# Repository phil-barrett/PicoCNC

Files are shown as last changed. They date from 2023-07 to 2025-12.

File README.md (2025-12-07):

# PicoCNC

## Now fully open source
I have released the full V1.55eth design files under the MIT open source license. Please post your usage and derivations in the [Discussions Section](https://github.com/phil-barrett/PicoCNC/discussions).

## older readme.
No longer available for purchase.

A breakout board that, along with grblHAL and a Rapsberry Pi Pico microcontroller, creates a powerful CNC motion controller for devices like routers, mills, lasers and lathes.  Using grblHAL, it forms the basis of a motion control system with advanced features.

[System builder's Resources](https://www.grbl.org/resources)

[User Manual](https://github.com/phil-barrett/PicoCNC/blob/main/PicoCNC%20User%20Manual.pdf)

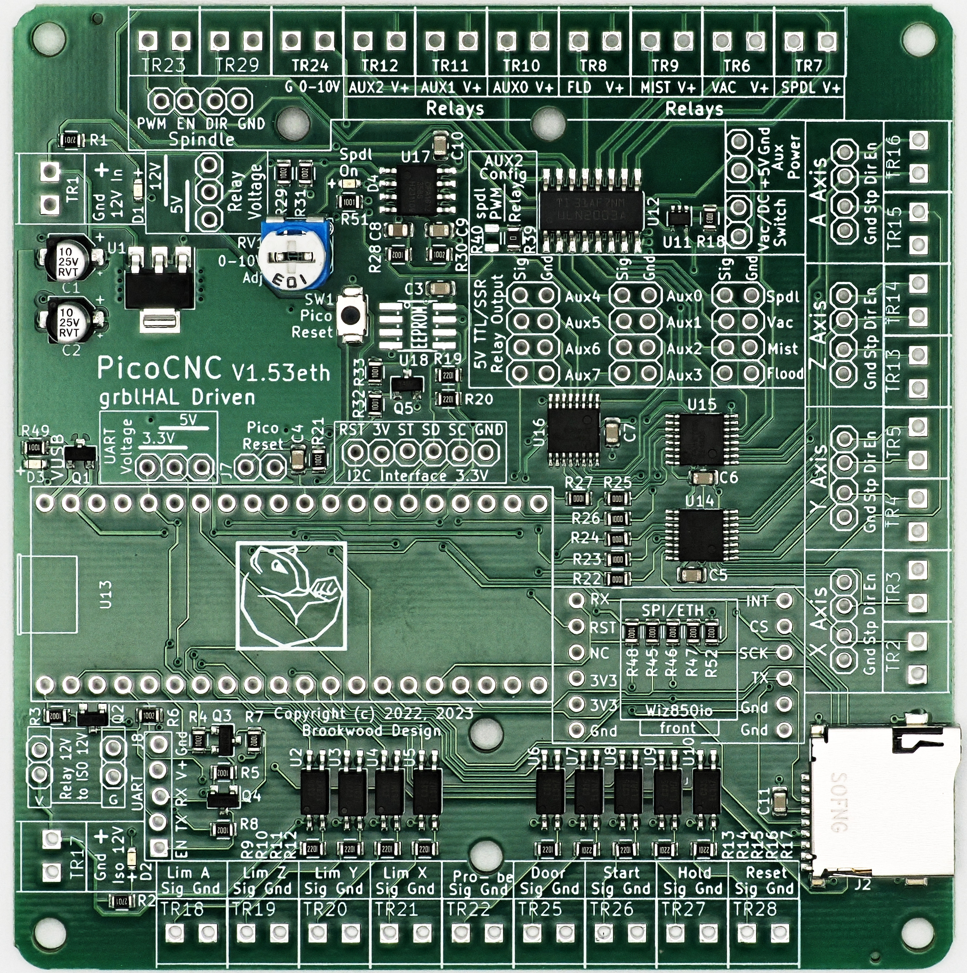
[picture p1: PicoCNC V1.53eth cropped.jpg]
PicoCNC


Key features of the PicoCNC board.
* Supports up to 4 Axes via Screw Terminal and Pin Header.
* Spindle control.
  - PWM (5V).
  - Direction (5V).
  - 0-10V.
  - 12V PWM supported (via open collector output).
* Limit Switches for each axis.
  - Supports switches or powered proximity sensors.
  - 12V for better EMI immunity.
  - Separate power input for full isolation
  - Opto-isolated
* Relay support
  - Directly drive up to 7 relay coils via open collector outputs.
  - Relay Coil voltage selectable between +5V or +12V.
  - Drive up to 11 SSR or Logic Level relays.
* Isolated standard Grbl input controls: Cycle Start, Feed Hold, EStop and Safety Door. Opto-Isolated.
* Opto-Isolated Probe input.
* Supports both Pico and Pico W.
* Comunications.
  - USB (via Pico and Pico W)
  - WiFi (via Pico W)
  - Ethernet (via Wiz850io Ethernet Module)
* Micro SD Card socket.  Allows storage of GCode programs.  GCode programs may be run from the SD Card.
* Dust Collection support.
  - Dust Collection relay and TTL output ganged to Spindle. 
  - Header for a switch to manually run Dust Collector.
* Flexible power input.  Two 12V sections, one for Stepper/Servo output, relays and spindle control, one for isolated limit, probe and control inputs. The two sections may be joined for the budget conscious builder. On board 5V generation.
* LED indicators for 12V inputs, +5V and spindle active.
* Open collector outputs allow adding pull-up resistors on the board.
* Expansion headers for I2C, SPI and UART.  UART 3.3V/5V translation supported.
* Powered by open source software - grblHAL.

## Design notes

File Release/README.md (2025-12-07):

## MIT License release of PicoCNC design files.

Copyright (c) 2023, 2025 Phillip L. Barrett

Permission is hereby granted, free of charge, to any person obtaining a copy
of this software and associated documentation files (the "Software"), to deal
in the Software without restriction, including without limitation the rights
to use, copy, modify, merge, publish, distribute, sublicense, and/or sell
copies of the Software, and to permit persons to whom the Software is
furnished to do so, subject to the following conditions:

The above copyright notice and this permission notice shall be included in all
copies or substantial portions of the Software.

THE SOFTWARE IS PROVIDED "AS IS", WITHOUT WARRANTY OF ANY KIND, EXPRESS OR
IMPLIED, INCLUDING BUT NOT LIMITED TO THE WARRANTIES OF MERCHANTABILITY,
FITNESS FOR A PARTICULAR PURPOSE AND NONINFRINGEMENT. IN NO EVENT SHALL THE
AUTHORS OR COPYRIGHT HOLDERS BE LIABLE FOR ANY CLAIM, DAMAGES OR OTHER
LIABILITY, WHETHER IN AN ACTION OF CONTRACT, TORT OR OTHERWISE, ARISING FROM,
OUT OF OR IN CONNECTION WITH THE SOFTWARE OR THE USE OR OTHER DEALINGS IN THE
SOFTWARE.

## Usage Notes

### KiCAD Files
These were created with KiCAD V8.0

They are released with the intent of using JLCPCB to manufacture the PCB and 
assemble them into a working circuit board. The directory production/ includes full gerbers (PicoU4XBB.zip), 
Bill of Materials including JLCPCB library part numbers (bom,.csv) and Centroid PnP (positions.csv).

### KiCAD plugins required
To create JLCPCB files after modifying the design, you will need the Fabrication Toolkit plugin. It is 
available in the KICAD Plugin and Content Manager.

### JLCPCB Library part numbers
These were current as of June 2025.  You may need to change due to out of stock parts.

## Questions, reports, suggestions

Please use the [Discussions section](https://github.com/phil-barrett/PicoCNC/discussions/34) to ask questions, report your progress or make suggestions.

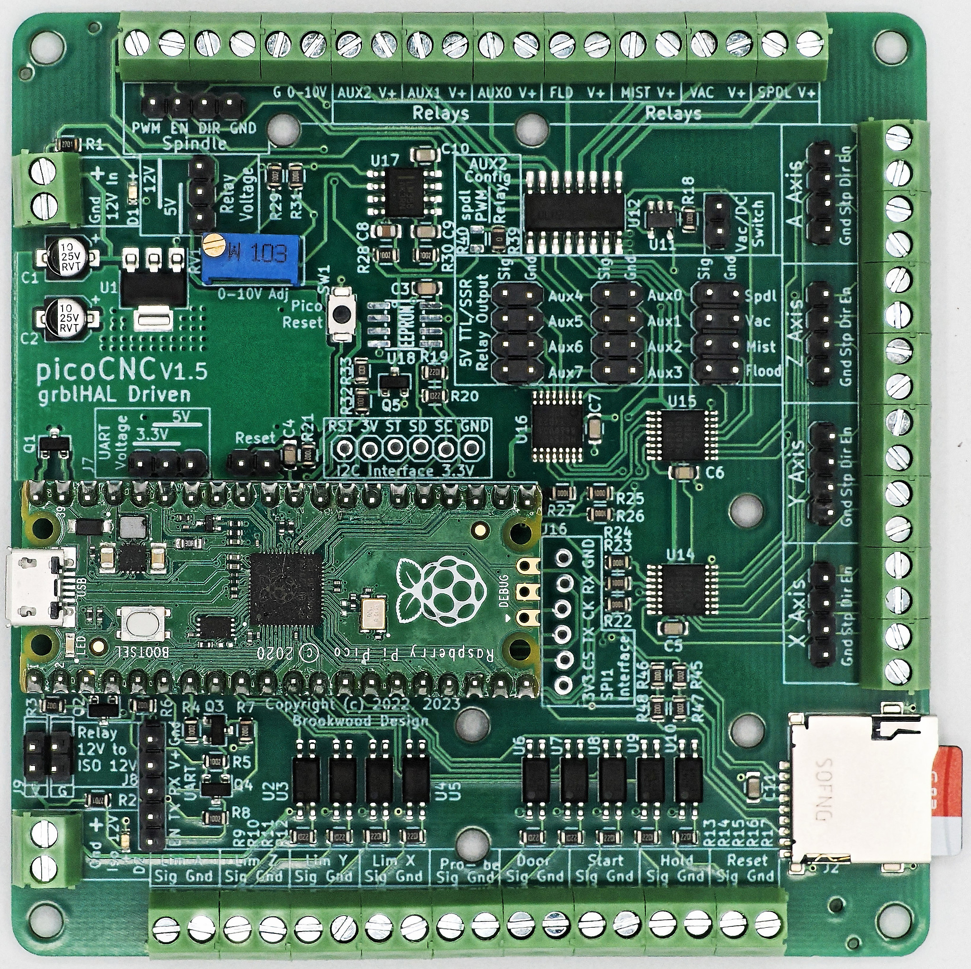
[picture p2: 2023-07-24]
PicoCNC.jpg

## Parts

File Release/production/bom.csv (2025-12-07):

Designator | Footprint | Quantity | Value | LCSC Part #
C1, C2 | 0805 | 2 | 10u | C15850
C10, C11, C3, C4, C5, C6, C7, C9 | 0805 | 8 | 100n | C49678
C8 | 0805 | 1 | 1uF | C28323
D1, D2, D3, D4 | 0805 | 4 | LED | C2297
J2 | sdcard_sofng_c111196 | 1 | MicroSD-MGnd | C111196
Q1 | SOT-23-rct | 1 | DMG2305UX-7 | C150470
Q2, Q3, Q4 | SOT-23-rct | 3 | BSS138 | C40912
Q5 | SOT-23-rct | 1 | MMBT3904 | C20526
R1, R2 | 0603 | 2 | 2K7 | C17530
R10, R11, R12, R13, R14, R15, R16, R17, R19, R20, R9 | 0603 | 11 | 2K2 | C17520
R18 | 0603 | 1 | 100K | C149504
R21, R28, R29, R3, R30, R31, R4, R45, R46, R47, R48, R5, R6, R7, R8 | 0603 | 15 | 10K | C17414
R22, R23, R24, R25, R26, R27 | 0603 | 6 | 100 | C17408
R32, R33 | 0603 | 2 | 1K | C17513
R39 | 0805 | 1 | 0 | C17477
R49, R51 | 0603 | 2 | 1K | C17530
R52 | 0603 | 1 | 4K7 | C17414
RV1 | RM065-trimmer | 1 | 10K pot | C5205021
SW1 | TA-1088R-02026 | 1 | SW_SPST | C455280
U1 | SOT-223-3_TabPin2 | 1 | AMS1117CD-5.0 | C277893
U10, U2, U3, U4, U5, U6, U7, U8, U9 | EL3H7-G | 9 | EL3H7-G | C92243
U11 | SOT-353_SC-70-5 | 1 | 74LVC1G32 | C460530
U12 | SO16 | 1 | ULN2003AD | C7512
U14, U15, U16 | HTSSOP-16_4.4x5mm_P0.65 | 3 | 74HCT595 | C460504
U17 | SO08 | 1 | LM358D | C2683482

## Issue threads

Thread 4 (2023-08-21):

D1 LED getting too much current

iLoveAndyBaker, 2023-08-21:
Minor nit-pick here, it seems like D1 and D2 are getting too much power (forward voltage is 2.71V), at least compared to the other LEDs on the board.  R1 and R2 are 2.7K, same as the resistor on all the other lines, but it's getting 12V and not 5V/3.3V etc.

D3 and R49 seem like a much happier combination at the lower voltage, the drop across it while on is 2.53V

phil-barrett, 2023-08-21:
Thanks for the note.  I believe all the LEDs are quite happy at their current levels.

While D1 and D2 do get more current than D3 and D4, (3.4 mA and 2.3 mA respectively) they are all well below the Max If of 25 mA for the 9-217/GHC-YR1S2/3T LED.  And, all 4 are well below the If they use for the specs (20 mA).  These modern LEDs are amazingly efficient. Back in the bad old days you had to pull 20 mA just to get a dim glow!
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

I had originally used 680 ohms for D3 and D4 which yields an If of 3.4 mA, I found that 1K gives about the same brightness level. This allows me to reduce the number of unique BOM items. Since I use a lot of 1K resistors, it makes the BOM cost slightly lower.

There are several other examples of BOM engineering in this board but I will leave it to others to find...

Closed 2023-08-21.

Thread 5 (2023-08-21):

U11 magic smoke and fire, Pi Pico W dead

iLoveAndyBaker, 2023-08-21:
U11 smoked, quite dramatically.  There is not and never was anything on the vac or dust collector.

Had steppers on X,Y,Z (with current limiting resistors on the step and direction pins) and only microswitches on X,Y,Z limits and a wire across reset.

Clean desk.

This is the second Pi Pico that this PicoCNC killed.

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

I suspect power issues on the board - , I haven't looked at the schematic however.  There was power cycling, I think it was probably my 12V (checked to 12.1V) supply resetting for an over-current situation until the chip got hot enough to go incandescent and stink up the whole room.  Thank god for the FR in FR4.

Things have been a little odd with powering it (can't really nail it down now that it's blowed up) but having to do weird power cycles here and there.

Please double check your power. Are we powering the Pico with the PicoCNC AND USB? Is Q1 working right? Did Tindie put the right part down?

phil-barrett, 2023-08-21:
Wow.  That's pretty dramatic.  I've been testing a number of these boards running on 12V power for a lot of hours and never had anything blow at all.  That device (74LVC1G32) runs on +5V and the pin that is burnt is the +5V pin.  Bad chip?  Maybe 12V got onto the 5V rail?  Could you show me a picture of the entire board?

Please return the board and we will refund your purchase.

iLoveAndyBaker, 2023-08-21:
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

Let me know where to mail it and I'll get it out soon.

phil-barrett, 2023-08-21:
Phil Barrett
76 Olympic Dr NW
Shoreline, WA 98177

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

phil-barrett, 2023-08-22:
I have been looking at the design for how this could happen and I really can't see anyway for that part to go short unless it was a bad part.  This circuit is in two designs with over 1100 units in the field and no reports of a problem.  I see several possibilities - 1) bad chip with an internal short (very rare), 2) shorting across the output (not obvious from the photos) or 3) chip damaged due to 12V across the 5V rail (hard to do accidentally).

iLoveAndyBaker, 2023-08-22:
Nothing, huh? Yeah I don't know either. Maybe something etched weird. Maybe a part was just bad, or wrong, or just randomly latched up. Either way, it's in the mail, I've thrown in the blown Pico as a bonus. I hope you can learn something from it, it looks like a nice little board. I would have liked to have put the FLIR camera on it, but as luck would have it, I've lent it out.

Thanks,

Andy

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

phil-barrett, 2023-08-30:
I got the board and did some poking. Powered it up with 12V.  The first thing that became clear is there was 11V on the 5V rail.  That pretty much blew all the 5V logic chips and the Pico.  I'd guess U11 being so small, it went first.  Looking at the 5V regulator U1 (AMS1117-5), I could see some damage to it. See the photo. (I made the scratch probing at it.) It failed with a direct short which is unusual - they usually die open. Maybe it took too much current and blew. Maybe too high voltage was applied - 24V would have killed it. Maybe reversed polarity? I looked at all the boards I have in stock (55) and none of them showed any damage to the regulator.  I desoldered the dead regulator and soldered a new one in place.  It happily produced 5V and did not overheat.  I did not see any evidence of over current any other place than U1 and U11.  So, it's hard to say what damaged U1.  I desoldered U11 and inspected the traces under it.  They appear to be ok so it wasn't a board short.  I also looked at the pin headers used to join the 2 12V sections to see if the shorting plugs had been installed wrong but did not see any damage.

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

So what did I learn from this?  To be honest, not a lot. A lot of this circuitry is the same as on the Teensy board. And the circuit is pretty straightforward. There is no obvious design flaw. I am thinking of adding an in line rectifier before the 12V input of the AMS1117 to at least protect it from reverse polarity though that has implications on the 0-10V circuit.  I had already separated the headers for joining the 2 12V sections to prevent accidental shorting (that's in V1.51, the currently shipping board). I am adding warnings to the User Manual about reverse polarity and power sources above 12V.

Anyway, I believe this is an isolated case.  There have been no other reports of a similar nature and in all the testing I never saw any significant overheating (I do a lot of thermal measurement on the boards during testing). In general, the worst case temperature increase is 15C over ambient, well within expectations.

Anyway, I have issued a full refund. Sorry this happened.
Phil Barrett

iLoveAndyBaker, 2023-08-30:
I'd be happy to take a new one to be honest. It makes my wiring a lot cleaner too.

The power supply was a nice switching wall wart putting out clean 12.1V.  It was running well, I connected it when I started the project and never looked back. As to why I was thinking those LEDs too bright, maybe it was that regulator after all. At any rate, I can use a different PSU.

I've seen people put big fat diodes across the input.. blows the fuse in the PSU if you go backwards, and no voltage drop that way. Provided it's got a fuse that is.

Thanks for looking into this.

Andy Baker
Red 6
________________________________
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

phil-barrett, 2023-08-30:
With the refund, you could place another order. Tindie is prompt about refunds.

phil-barrett, 2023-09-02:
I'm closing this. There have been no more reports of anything similar so I am calling a one-off problem. If anything comes up I will reopen.

Closed 2023-09-02.

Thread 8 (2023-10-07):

BOM?

pixelwaster, 2023-10-07:
The parts list on page 33 is missing. I would like to experiment with this controller.

Michael

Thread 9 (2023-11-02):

Brake Out Board for Blackpill (STM32F411CE - WeAct Studio)

wolfgangbregel, 2023-11-02:
Hello Phill,

I much appreciate your work and the well designed BOBs for Pico and Teensy.

Just a proposal: Why not consider the low cost Blackpill (STM32F411CE - WeAct Studio) as a controller base?

* Well supoported by GRBL HAL (Flawless compile with STM32Cube Ide - or GRBL Web builder)
* Just enough GPIOs (a total of 32 +2 used for SW-JTAG)  for a 4 or 5 axis CNC including per axis limit switches and inputs for Safety Door, Feed Hold, Cycle Start, Reset E-Stop and Probe
* Outputs for Spindle (Dir, Enable, PWM), Coolant Flood and Mist
* Optional inputs for Spindle Pulse / Index
* No need for external serial->parallel Expander chips at high speed clocks
* Integrated USB CDC
* Works just fine on my CNC metal milling machine (On my home brew breakout board for now)
* Plenty of headroom in Ram amd Flash for extensions and future development

Many thanks for considering,

Wolf

phil-barrett, 2023-11-02:
Thanks for the input.  As usual, there are always trade-offs to be taken into account. Such is engineering...

I've considered the Black Pill before and it would be a very reasonable choice on many fronts.  One problem is that Chinese suppliers often change components without any notice.  This includes the actual processor (there are a number of F411 clones out there that MOSTLY work the same as the STM part).  Also, the availability of the Black Pill is highly variable. I have looked at using the F411 directly on a base board but the chip shortage hit the STM32 line very hard. The RP2040 never had that problem and it is a consistent product, never any silent changes. As we emerge from the still lingering effects of the shortage, I will continue to re-evaluate things.

The main difference is that the PicoCNC board only supports 4 Axes. The PicoCNC step output rate is well above 200 KHz, supports WiFi, doesn't need a programmer and is super inexpensive.  Not suitable for lathes, though. And, soon I will release a PicoCNC that will support Ethernet.  A Blackpill based board with Ethernet would probably not be able to support 5 Axes in that case.

wolfgangbregel, 2023-11-02:
Hello Phil,

Yes, I fully understand your concerns as to chinese suppliers and their
liberty in changing specs and/or chips.
And yes the Pico is well documented and more consistent over time since its
appearance.
I want to replace an Arduino based control board (i.e. no interference
protection - but no EMC problems either) in order to have a 4th axis and
backlash compensation.
So - I'll order one of your PicoCNC boars shortly. I just had a few really
annoying surprices from the German customs dept. I.e. calling for next to
half of the invoice as import tax for electronics received from the US.

Greatings and thumbs up from Germany

Wolfgang

On Thu, Nov 2, 2023 at 4:44 PM phil-barrett ***@***.***>
wrote:

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

phil-barrett, 2023-11-02:
Thanks!  I have a lot of German customers, it is my second biggest market (after USA), and have not heard them complain about getting nicked for customs/duty/VAT. I do supply correct documentation including price so the max should be a 20% charge, I think. (I will admit, it's hard to keep track of it.) Maybe they just don't tell me. Note, I use the US postal system which hands off to Deutsche Post and not carriers like FedEx or UPS. The few times I have used UPS internationally they not only hit the customer for Duty/VAT and ignored the listed price but also added a $30 or so brokerage fee. One Irish customer was charged $70 on a $70 order. Thieves.

wolfgangbregel, 2023-11-03:
Hello Phil,

many thanks for your info. Indeed, Deutsche Post/DHL is the most reliable,
honest and mostly cheapest service here in Germany.
Good to hear that US postals works with DHL only.
I once had an experience with UPS for an order I accidently placed with
DigiKey US. I had to pay about $20 service fee on the $50 order - heavy
(plus VAT of course).

So i checked for orders from the US to Germany *below *€150 (*above *is
different):

Duty: None
Import VAT: 19% (on the invoice total, incl. transport!)
DHL service fee: €6

Just for info, in case someone asks.

I'll order a PicoCNC via Tindie shortly.

Many thanks for the great job!

Best regrards, Wolfgang

On Thu, Nov 2, 2023 at 8:35 PM phil-barrett ***@***.***>
wrote:

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

wolfgangbregel, 2023-11-03:
Hello Phil,

just to let you know: I just ordered a PicoCNC assy kit via Tinide.

Best regards, Wolfgang

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

phil-barrett, 2023-11-03:
Thank You.

You should have email confirmation and the package will ship in about 1 hour.

Phil

wolfgangbregel, 2023-11-03:
Hello Phil,

yes, just received a confirmation from US postal.

Many thanks, Wolfgang

On Fri, Nov 3, 2023 at 5:47 PM phil-barrett ***@***.***>
wrote:

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

Closed 2024-02-16.

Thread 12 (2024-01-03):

Best way to buy from Europe (Italy)

yaapu, 2024-01-03:
Hi Phil,
I'd like to get one of your PicoCNC boards, I tried tindie but the only shipping option is "United States Postal Service Standard Ground Rate (No Tracking)", I'd rather use a tracked service since custom duties are involved, do you have any hints/ideas?

phil-barrett, 2024-01-03:
Actually, you will get tracking with that service.  I should revisit the tindie shipping setup.

phil-barrett, 2024-01-03:
Fixed it.  Now it says tracking.

Note that this is a US Postal Service tracking number and may not give you tacking within Italy.  I have seen cases in a number of countries where tracking is not updated after the hand over to the local postal service.  And, I have seen cases where a given country's tracking is inconsistent - sometimes they do it but other times they don't.  Very annoying and there is no recourse.  Sorry, I wish it was better.

Phil

yaapu, 2024-01-03:
Thanks for your super quick reply, I suspect that international orders will not use Ground Service, do you have an idea of which tracked service will be used?
Any track record of how long it would take to get it to italy or europe?

phil-barrett, 2024-01-03:
USPS hands the package off to whatever the designated carrier is for the end country.  Usually it is the national mail carrier but I don't have any visibility into that.

Ship time to EU countries can vary a lot.  1 week to 4 weeks. The last several I shipped to Italy ranged between 13 and 17 days. Once the package gets to Italy, it appears to take just a few days.  The biggest delay for international shipping is the gap between the last US reported location and the first end country location.  That is between 3 and 10 days, typically.

yaapu, 2024-01-03:
Thanks Phil

Closed 2024-01-03.

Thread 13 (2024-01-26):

When will you get the assembly kit back in stock?

rgfx, 2024-01-26:
Sorry for posting here. I want to order one of these but have the kit would be nice. I can wait.

phil-barrett, 2024-01-26:
Oops.  Thanks for posting!  I don't get notifications when options go to zero.  Had plenty of kits, my bad for not keeping an eye on it.  Fixed!

Closed 2024-02-16.

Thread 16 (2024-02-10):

Ethernet + sdcard + i2c panel

pimsierhuis, 2024-02-10:
We like to use ethernet, sd card and use an i2c keypad, so we're running into the error "I2C strobe pin not available, is assigned as ethernet IRQ!". Could there be any chance of supporting that configuration? I think it could be a quite useful use case.

phil-barrett, 2024-02-10:
I totally agree - a very useful case. Unfortunately, the Pico just doesn't have enough pins to support both. I am working towards supporting that scenario on the next version of the PicoCNC as it will use the RP2040 directly and get a few more pins - I2C and Ethernet concurrent are absolutely the top priority.  We are at least 6 months from that being available.

An alternative is to use the Teensy version which does support Ethernet, SDCard and I2C concurrently.

Another possibility if you are designing the keypad HW is to use the UART.

Phil

pimsierhuis, 2024-02-11:
OK, thanks for your explanation!

Will stick with a panel via UART for now then, can always upgrade later.

Closed 2024-02-16.

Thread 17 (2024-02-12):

Ethernet on v1.52

JelmerV, 2024-02-12:
Hi, I bought 2 PicoCNC boards just before the update that added the Wiz850io header. However, I realize Ethernet will be very useful and would like to add it.

Do you have any advice on wiring it and configuring the Wiz850io on a PicoCNC V1.52?

phil-barrett, 2024-02-12:
It is possible but messy.  You would need cut a few traces and add 3 bodge wires.  In addition, you would need a way to secure the Wiz850io.  I would be willing to give you a 20% discount on replacement boards/kits if you would prefer. Shipping cost will be better, too. Talk to me directly, not through Tindie.

If you want to go the bodge wire approach, let me know and I will write something up.

JelmerV, 2024-02-12:
Thanks for the offer! However for the time being I would prefer to work with the older boards that I've got. If you could just share which connections to make that would be enough. I have some additional circuitry to add on perfboard anyway so securing it shouldn't be a problem.

phil-barrett, 2024-02-12:
OK.   I will write it up in the next day or so.  I may do a blog post.  Look in the discussions section for either the write up or a pointer to the blog post.

phil-barrett, 2024-02-16:
Posted on Discussions.

Closed 2024-02-16.

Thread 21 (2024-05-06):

24v support

freexperia, 2024-05-06:
many CNC and printer projects use 24V for both steppers and control boards to reduce the need for an additional 12V PSU.

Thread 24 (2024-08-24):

Description of $14 in user manual

WheeSci, 2024-08-24:
The suggested value for $14 on page 15 of the user manual (15) does not work.  I understood the text to mean that E-stop and Reset were separate pins and required mask values of 1 and 8 to invert.  In fact, I now believe (after reading [this](https://github.com/grblHAL/core/wiki/First-Run-Grbl-Settings) and trying it on my own) that the E-stop and Reset share a pin and that its inversion value is 64.  Thus, the inversion mask value to invert all pins should be 70.  My issues trying to resolve this are in [this reddit](https://www.reddit.com/r/hobbycnc/comments/1eyx9hj/raspi_pico_not_accepting_change_to_grblhal/) thread.

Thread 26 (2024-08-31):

Gerber files

matta-pie, 2024-08-31:
Hi! Would it be possible to open source gerber files? I would like to cnc the board for a small project

phil-barrett, 2024-09-01:
At time, I do not plan to release the gerbers.  I may revisit that in the future, though.

Closed 2024-09-07.

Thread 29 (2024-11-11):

Using a lower voltage for the opto-isolated input

BenjaminPoilve, 2024-11-11:
I plan on using optical endstops on my machine, and they rely on pre-built board using 5V as signal level.
Am I right to think that I could just replace the 12V ISO input by a 5V power supply, and get on with it (with of course a significant reduction in EMI resistance)?
The led in the opto-isolator would get a bit less than 2mA, which is not great, but should be enough to pull the logic input down, and if not, I'd just have to replace the led resistors.

Is there anything else that I should keep in mind for that modification?

Thanks in advance.

phil-barrett, 2024-11-11:
I have not tested the PicoCNC with 5V iso voltage.  The resistors on the Opto Isolators are 2.2K.  With a nominal voltage drop of 1.2V, that leaves 1.7 mA flowing through the EL3H7 opto.  While this is not ideal, the datasheet suggests that it can work.  If you have problems (like EMI susceptibility), I would replace the resistors with 470 ohm (603 SMT) which would yield 8 mA opto current and a much more robust current transfer ratio. I can talk you through that if you need.

Your board went out in the morning mail drop to the post office, by the way.

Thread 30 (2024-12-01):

Pico 2 support?

Dexus, 2024-12-01:
Would this word support the pico2? Or only the pico1?

phil-barrett, 2024-12-01:
Yes, the Pico2 fits in the board.  Currently, there is not a version of grblHAL that supports it but I have heard that it may be coming.

Phil

phil-barrett, 2024-12-04:
We are making progress.  The Web Builder now supports building grblHAL for a Pico2 (RP2350) plugged into a PicoCNC board.  There are a couple of issues with timing for step generation that I think will be fixed soon.

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

Dexus, 2024-12-04:
Have seen it. Now I await my order be shipped ;) from US to DE. Thank you.

one more thing I would like to know it should be easy to use a diode laser on that board right? Or should I know something special?

Best Regards josef

phil-barrett, 2024-12-04:
[This might help](https://www.grbl.org/single-post/using-a-diode-laser-with-grblhal)

Dexus, 2025-01-17:
@phil-barrett only to be sure, i have to switch the 0 resistor from R40 to R39 right for laser mode?

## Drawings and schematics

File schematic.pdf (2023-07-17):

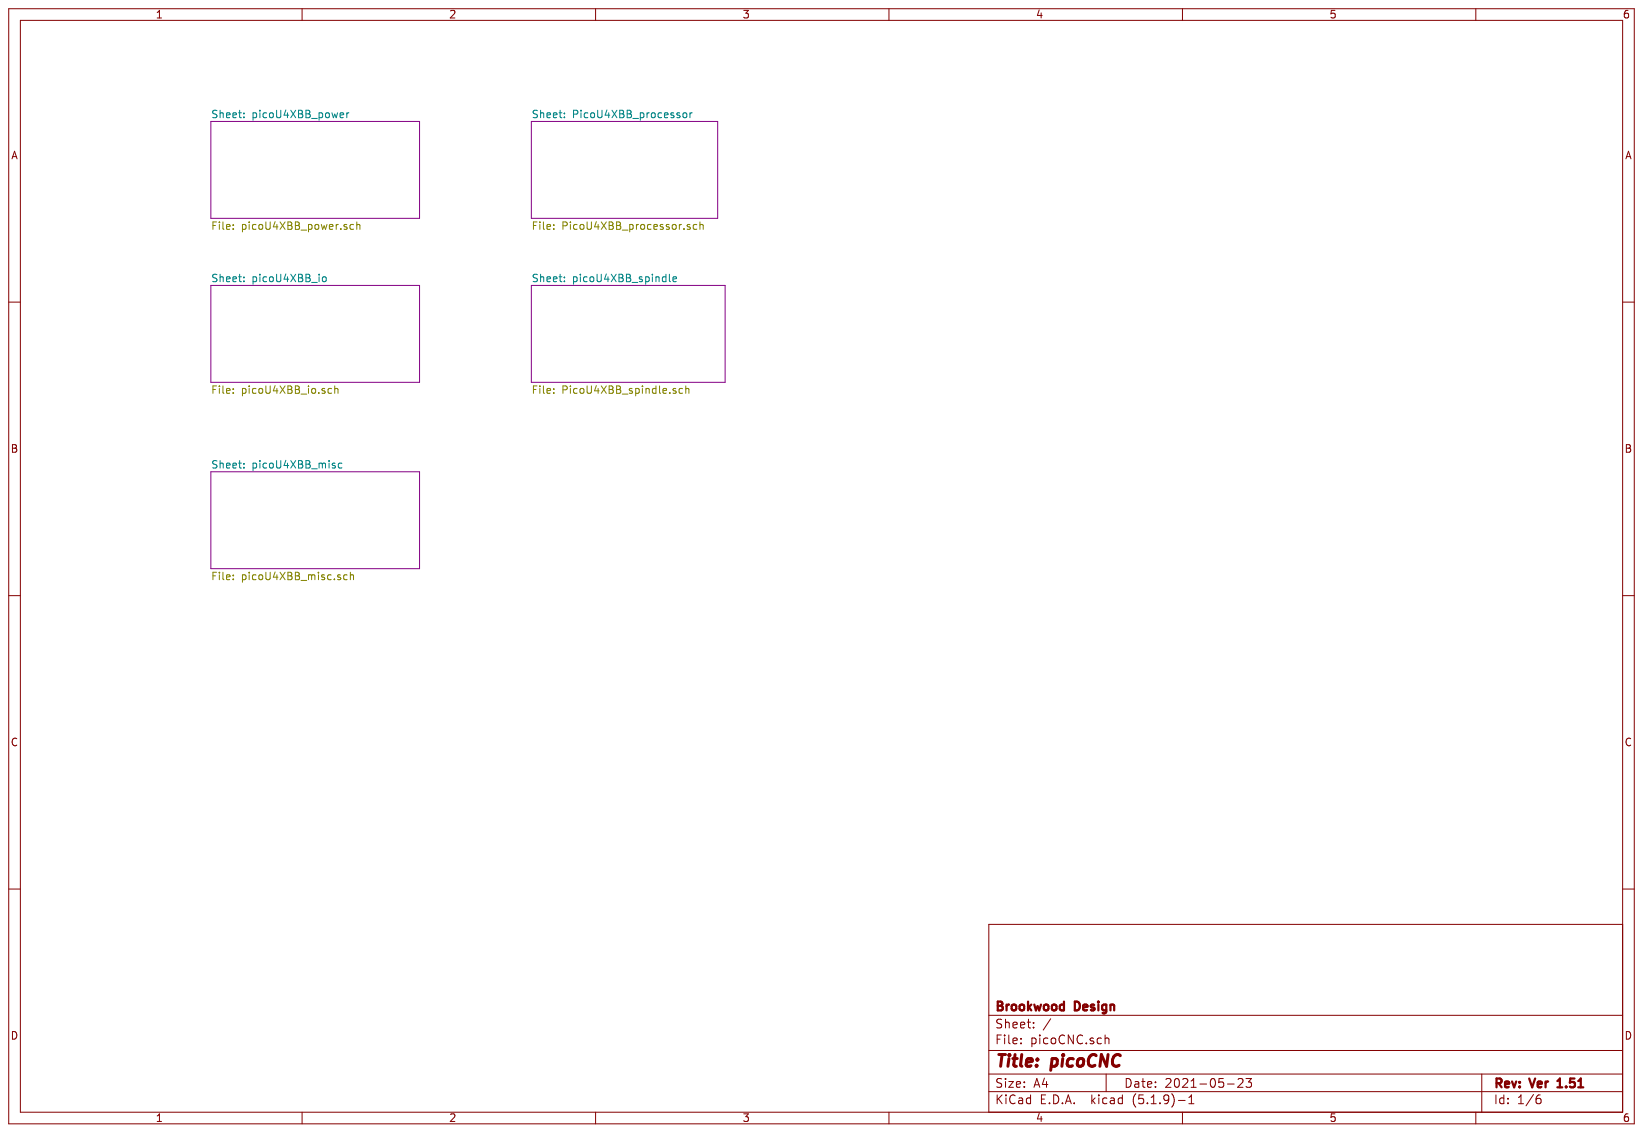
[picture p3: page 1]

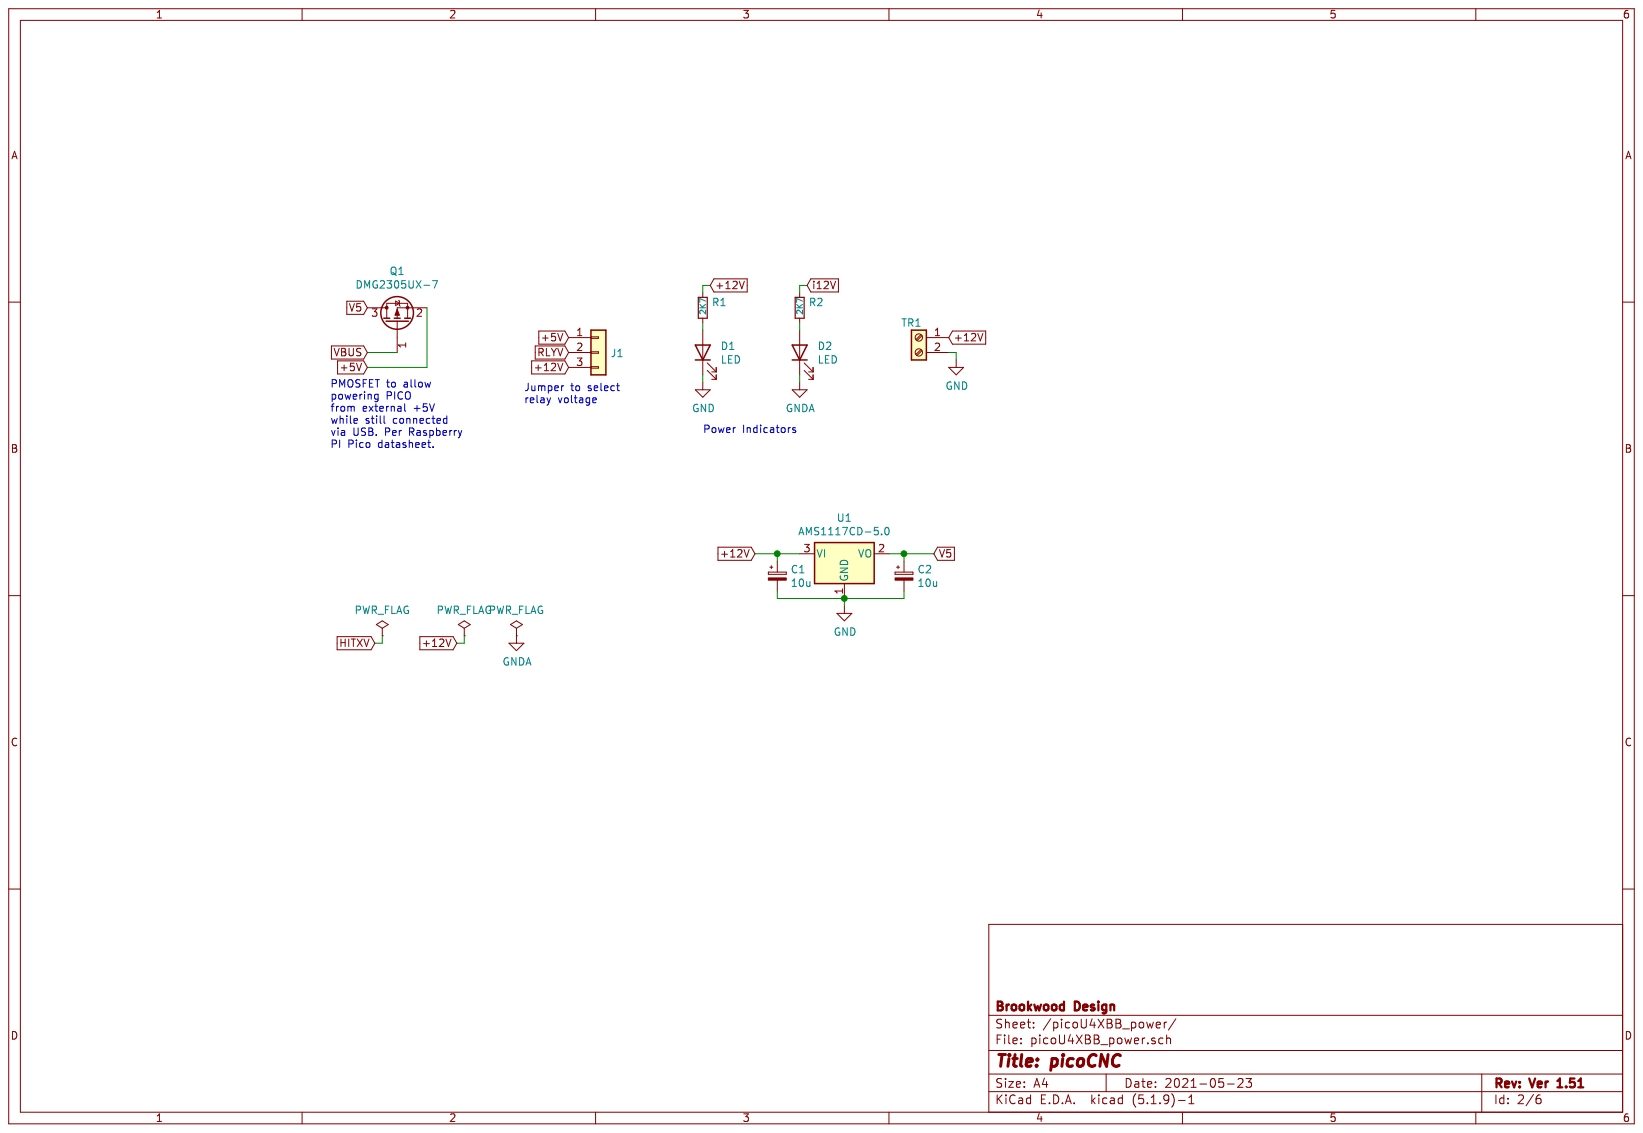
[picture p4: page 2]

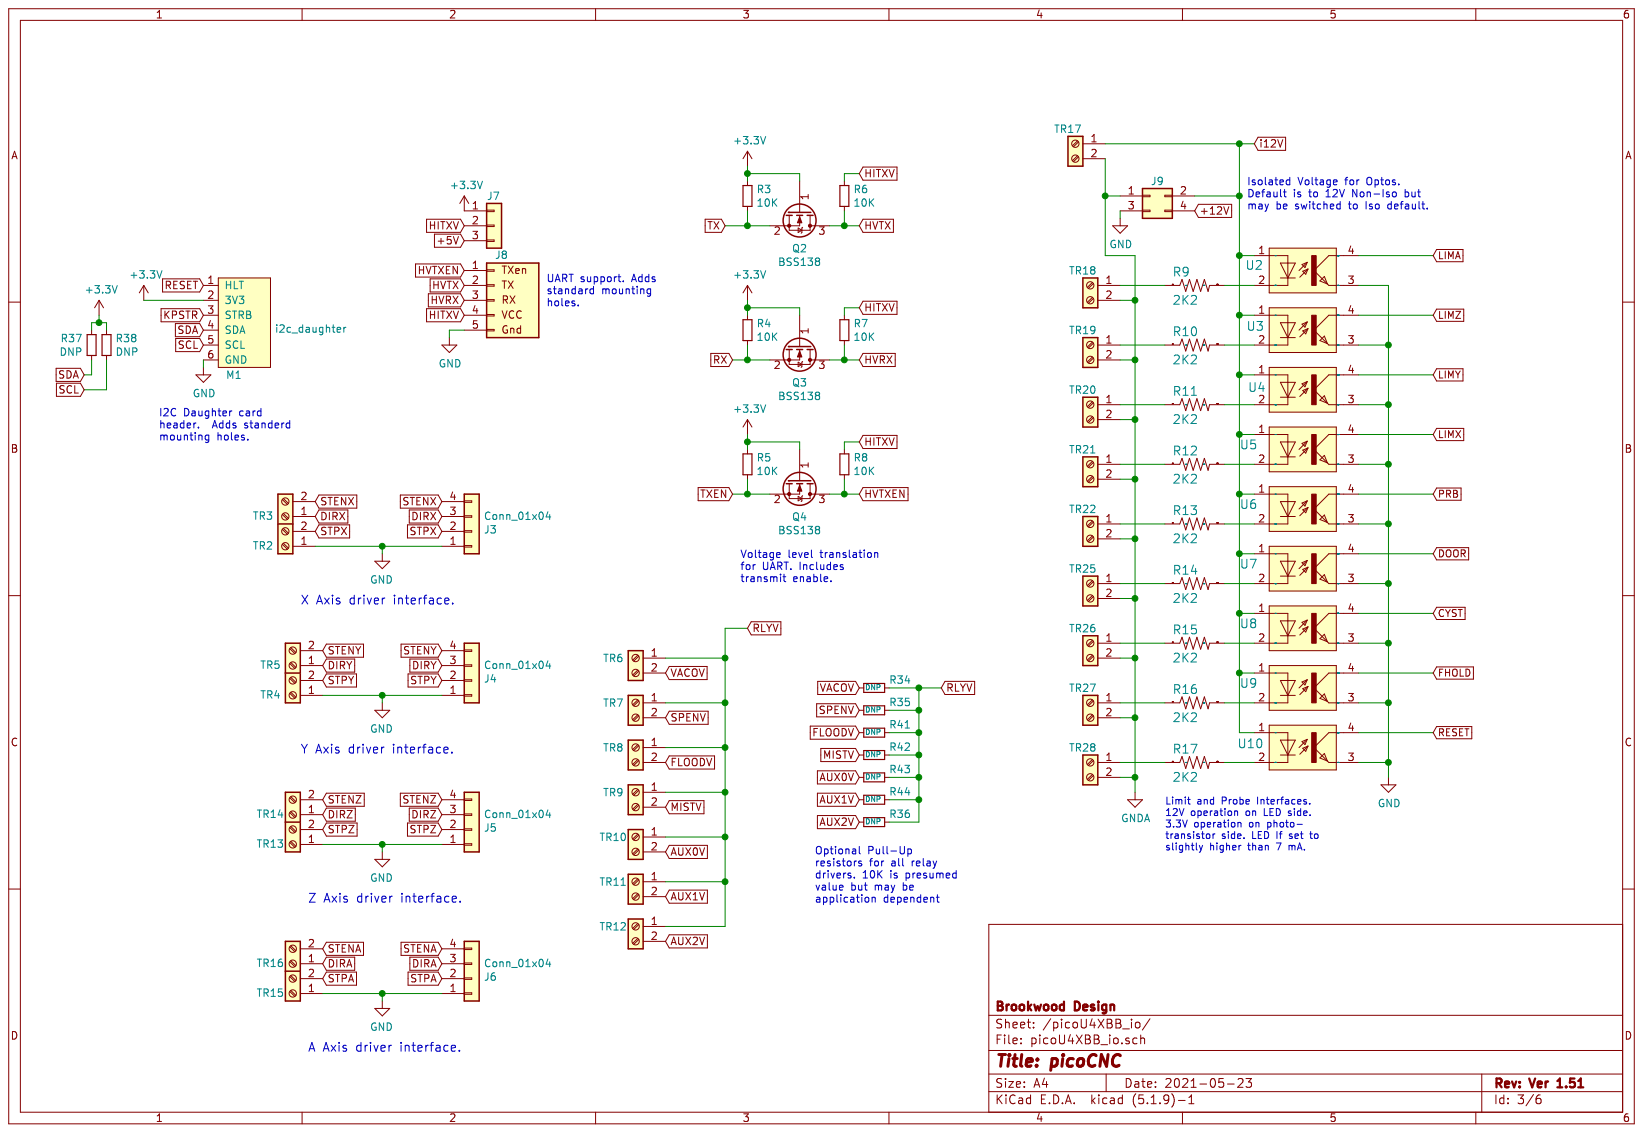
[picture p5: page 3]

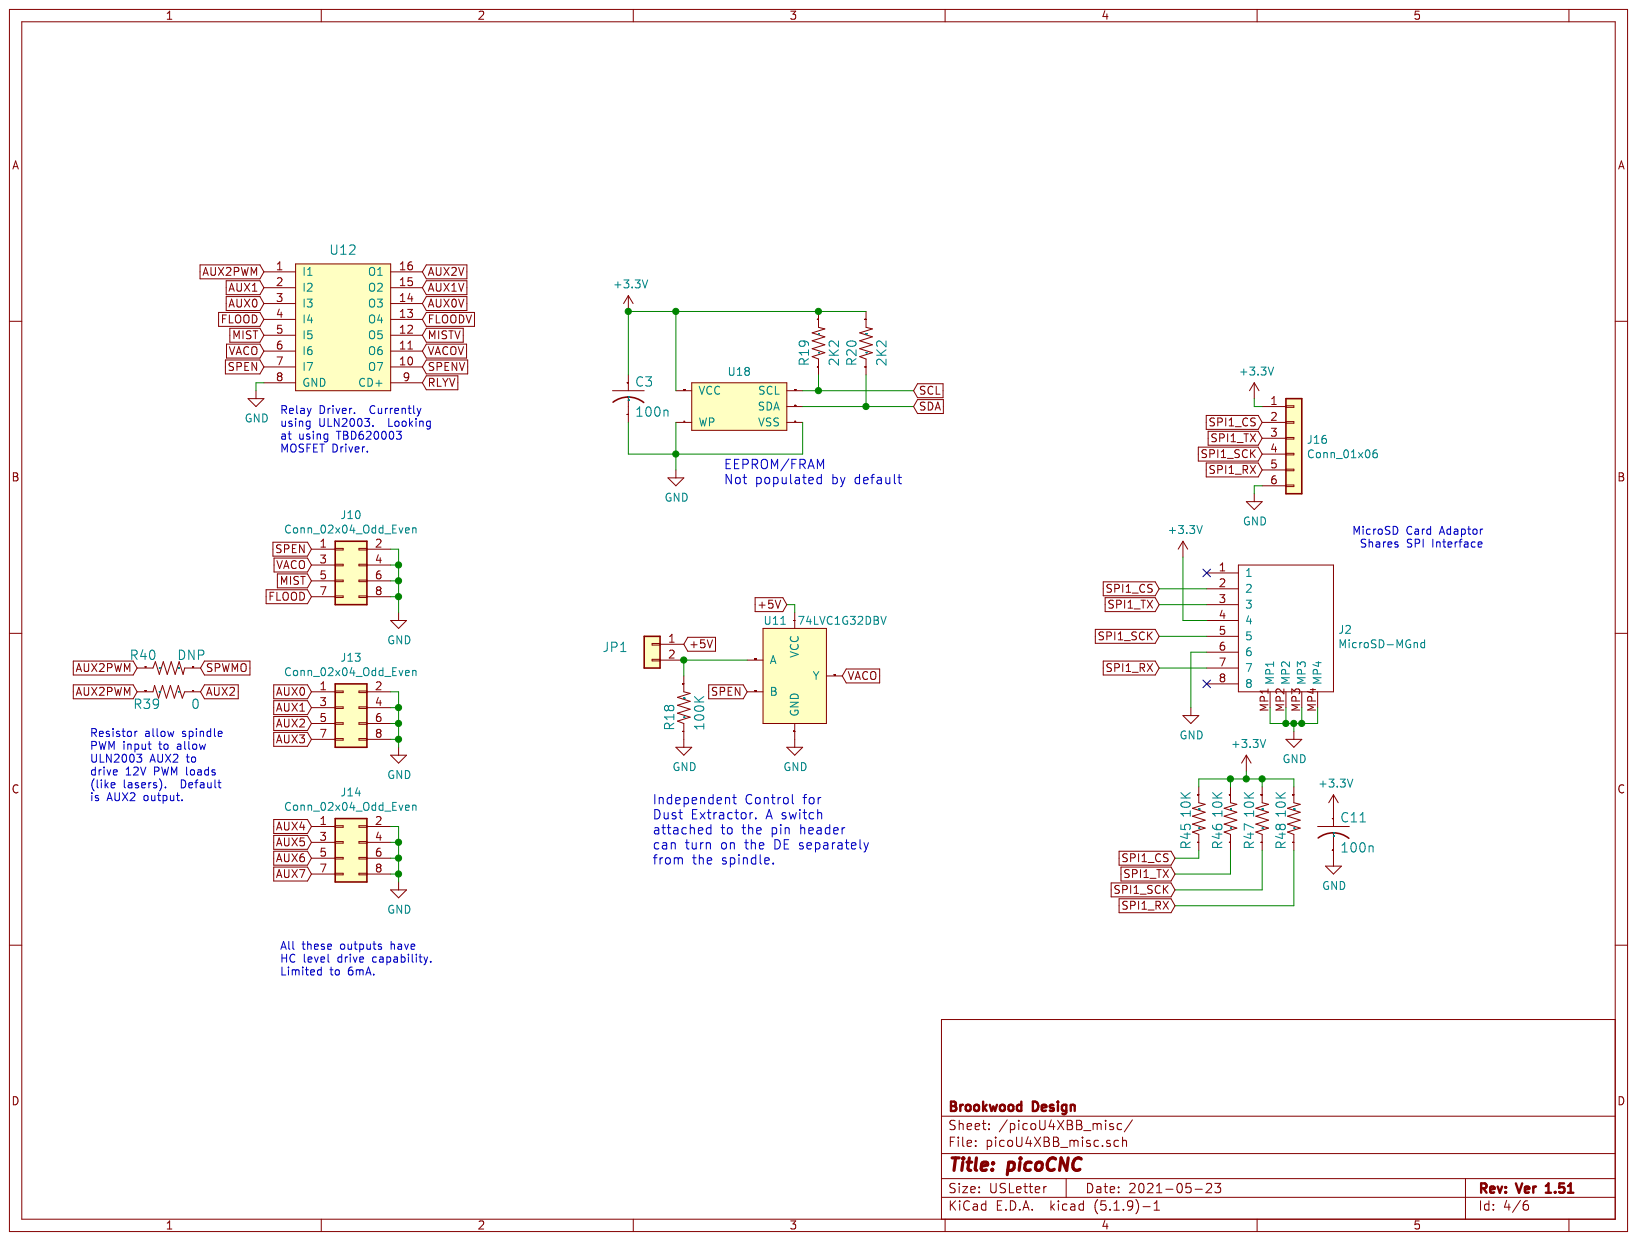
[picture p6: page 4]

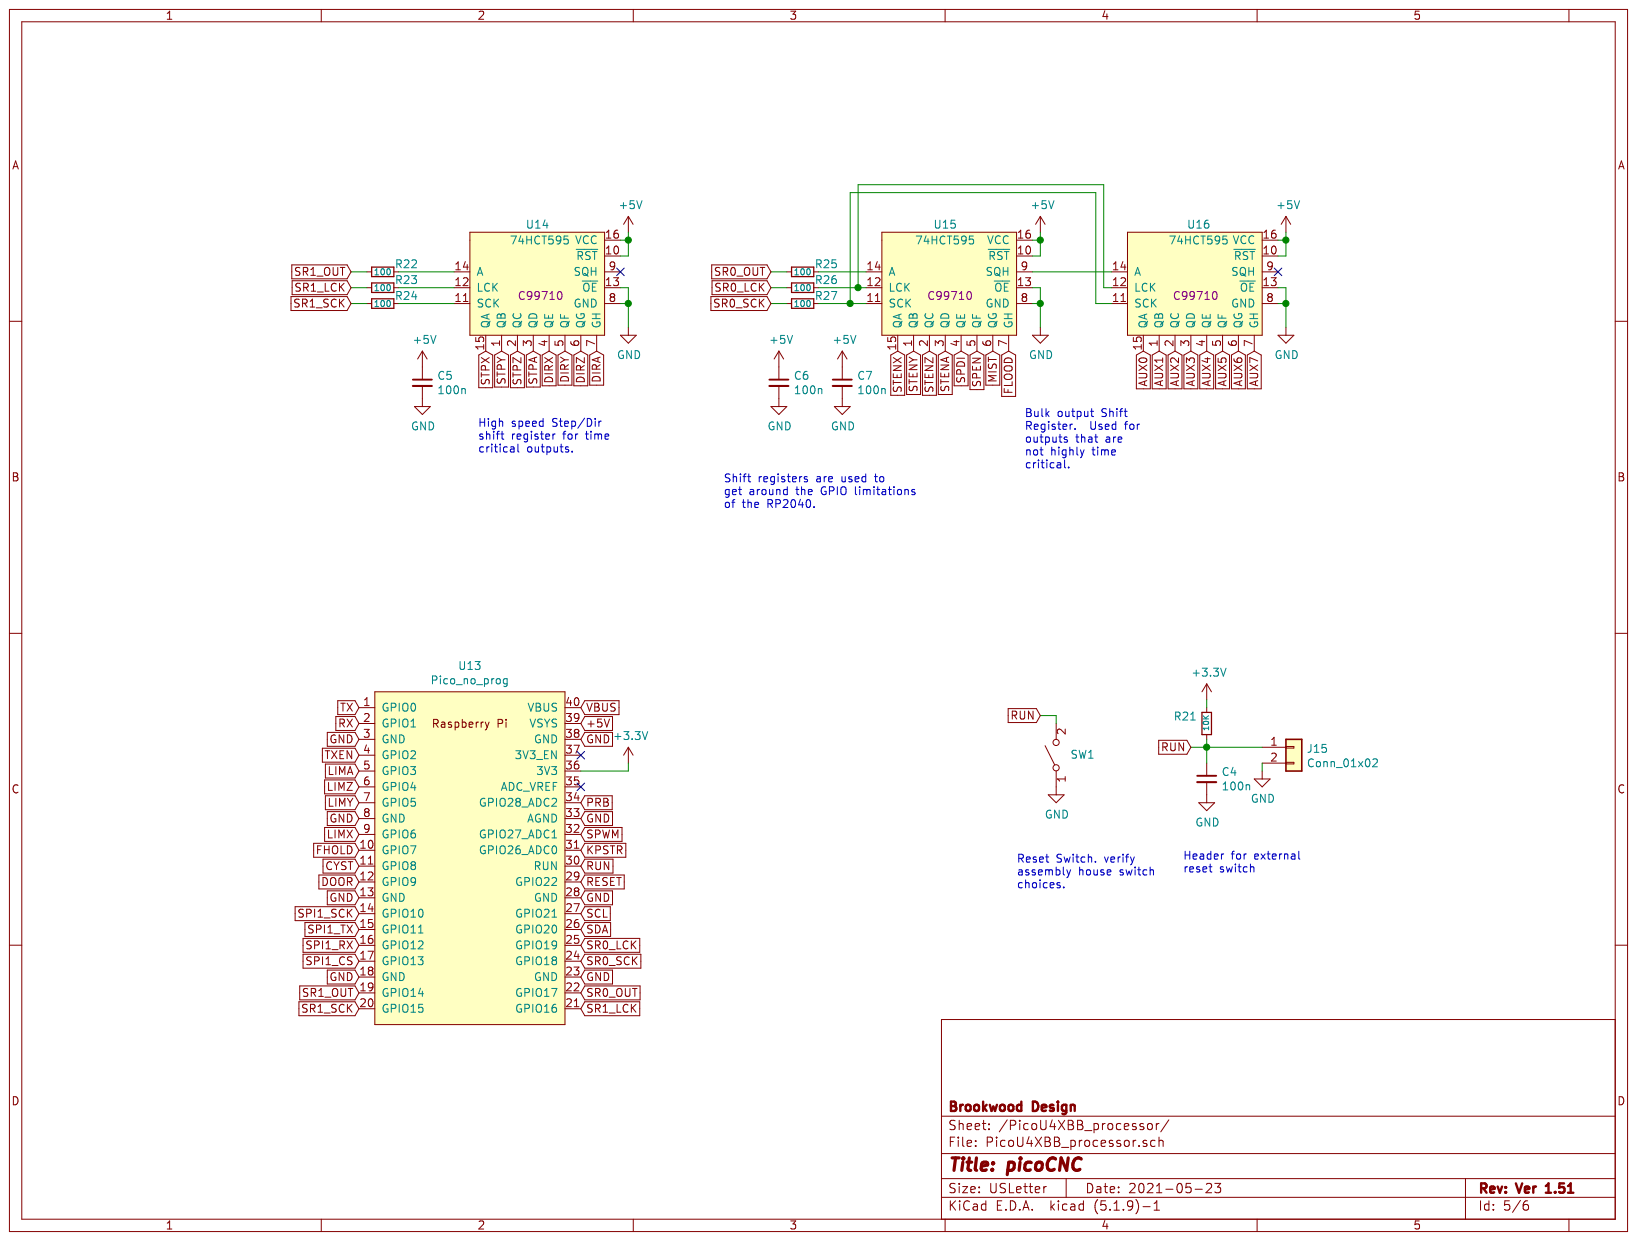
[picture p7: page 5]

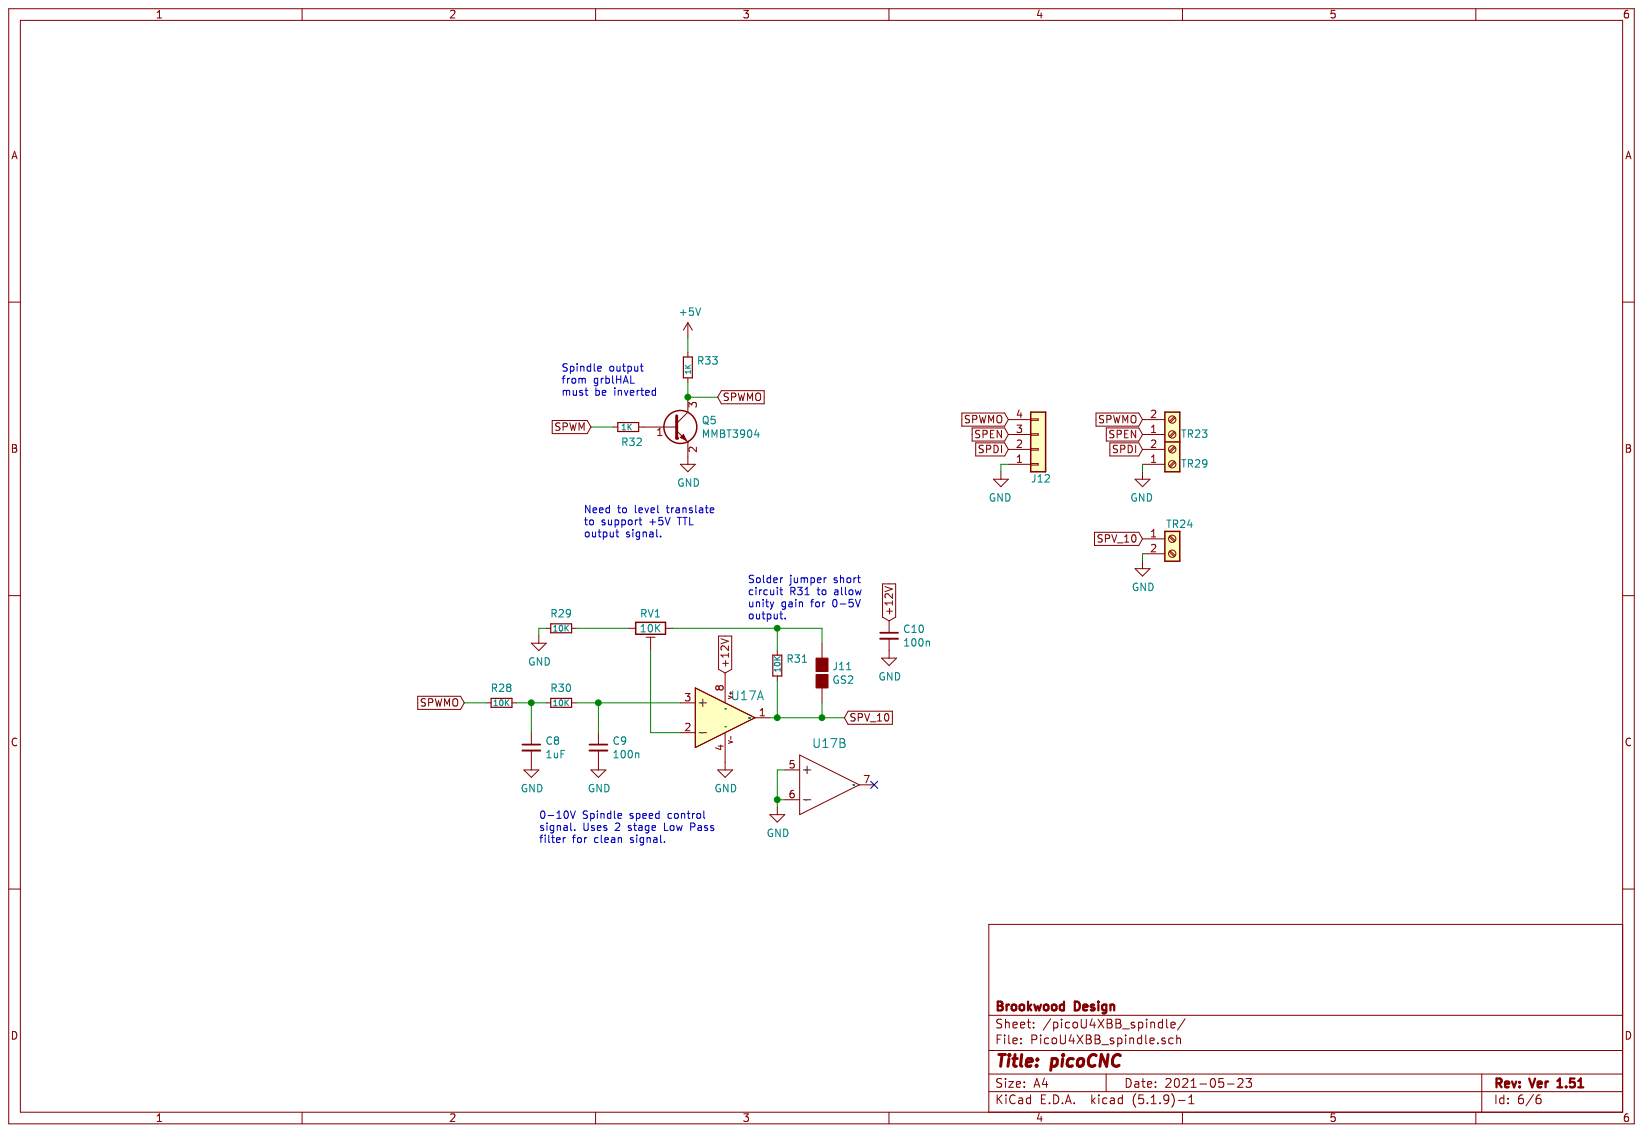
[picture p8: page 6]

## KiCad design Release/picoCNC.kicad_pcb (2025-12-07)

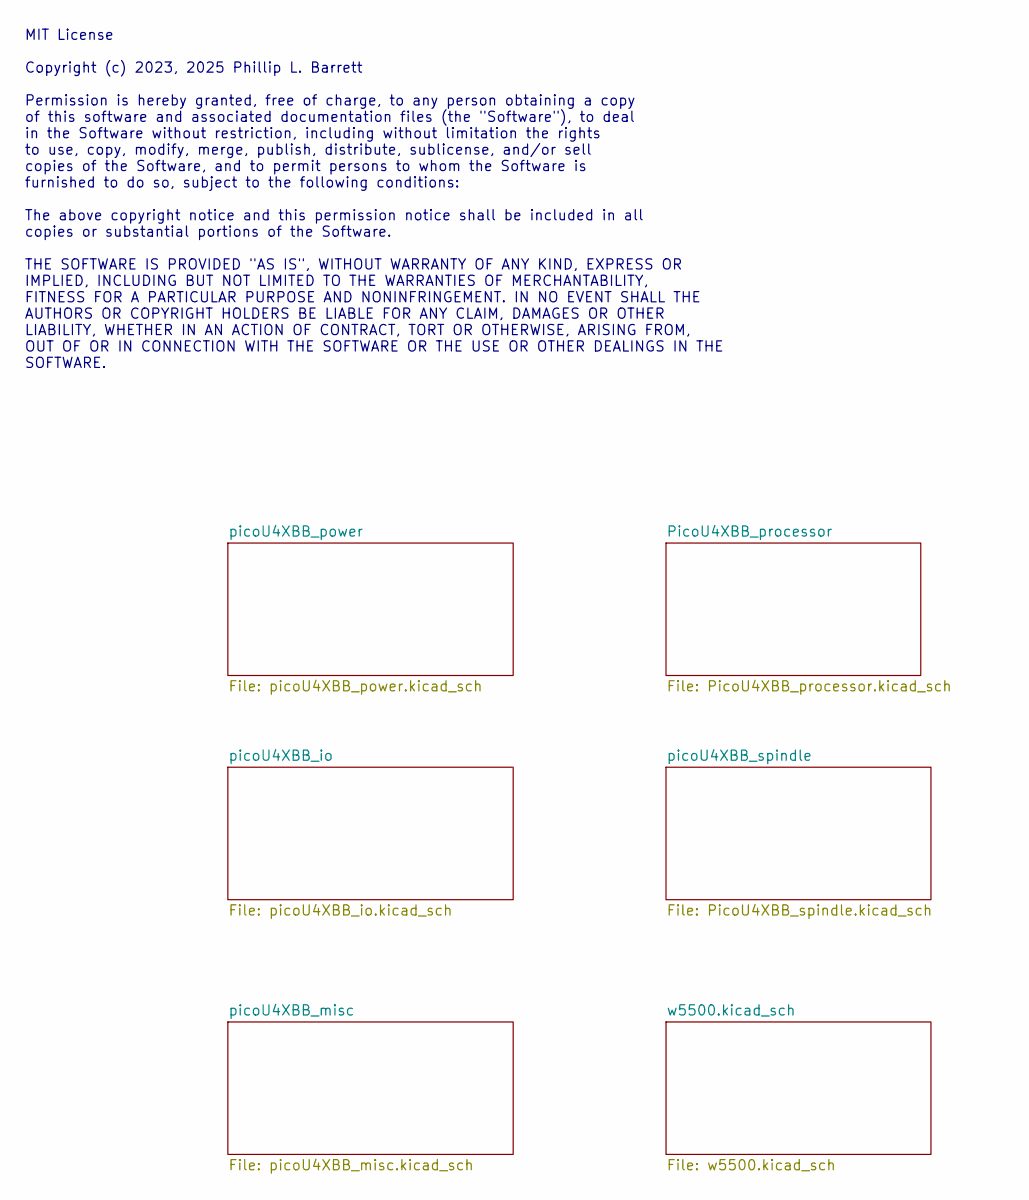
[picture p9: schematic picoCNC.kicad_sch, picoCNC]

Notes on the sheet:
MIT License Copyright (c) 2023, 2025 Phillip L. Barrett Permission is hereby granted, free of charge, to any person obtaining a copy of this software and associated documentation files (the "Software"), to deal in the Software without restriction, including without limitation the rights to use, cop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

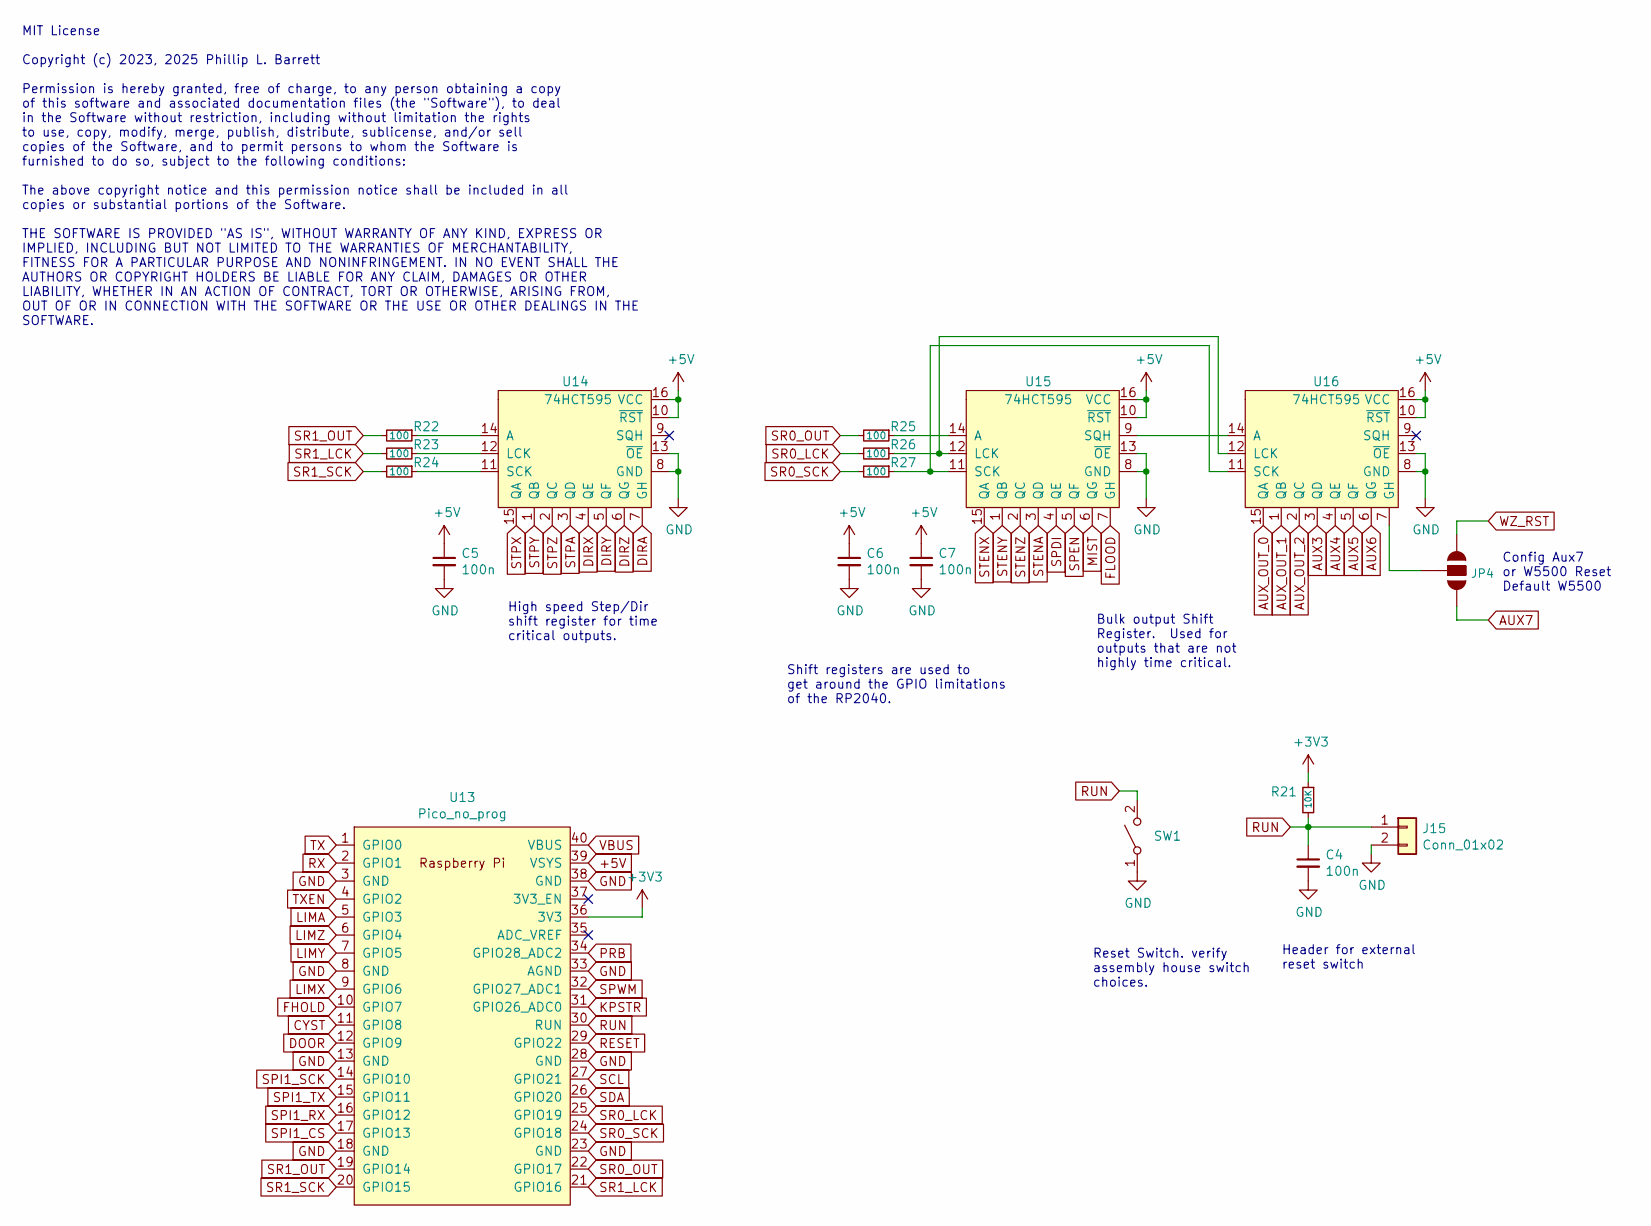
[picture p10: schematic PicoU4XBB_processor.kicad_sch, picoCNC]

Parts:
C4, C5, C6, C7: 100n; C_0805_2012Metric; LCSC C49678
J15: Conn_01x02; 1X02
JP4: JUMPER-SMT_3_NO_NO-SILK; SolderJumper-3_P1.3mm_Bridged12_Pad1.0x1.5mm
R21: 10K; R_0603_1608Metric; LCSC C25804
R22, R23, R24, R25, R26, R27: 100; R_0603_1608Metric; LCSC C22775
SW1: SW_SPST; TA-1088R-02026; LCSC C455280
U13: Pico_no_prog; RaspBerry_PI_Pico_no_prog
U14, U15, U16: 74HCT595; HTSSOP-16_4.4x5mm_P0.65; LCSC C460504

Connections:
+5V: C5.1, C6.1, C7.1, U13.39 (VSYS), U14.10 (~RST), U14.16 (VCC), U15.10 (~RST), U15.16 (VCC), U16.10 (~RST), U16.16 (VCC); also elsewhere on the board
AUX0: U16.15 (QA); also elsewhere on the board
AUX1: U16.1 (QB); also elsewhere on the board
AUX2: U16.2 (QC); also elsewhere on the board
AUX3: U16.3 (QD); also elsewhere on the board
AUX4: U16.4 (QE); also elsewhere on the board
AUX5: U16.5 (QF); also elsewhere on the board
AUX6: U16.6 (QG); also elsewhere on the board
AUX7: JP4.3; also elsewhere on the board
CYST: U13.11 (GPIO8); also elsewhere on the board
DIRA: U14.7 (GH); also elsewhere on the board
DIRX: U14.4 (QE); also elsewhere on the board
DIRY: U14.5 (QF); also elsewhere on the board
DIRZ: U14.6 (QG); also elsewhere on the board
DOOR: U13.12 (GPIO9); also elsewhere on the board
FHOLD: U13.10 (GPIO7); also elsewhere on the board
FLOOD: U15.7 (GH); also elsewhere on the board
GND: C4.2, C5.2, C6.2, C7.2, J15.2, SW1.1 (A), U13.3 (GND), U13.8 (GND), U13.13 (GND), U13.18 (GND), U13.23 (GND), U13.28 (GND), U13.33 (AGND), U13.38 (GND), U14.8 (GND), U14.13 (~OE), U15.8 (GND), U15.13 (~OE), U16.8 (GND), U16.13 (~OE); also elsewhere on the board
KPSTR: U13.31 (GPIO26_ADC0); also elsewhere on the board
LIMA: U13.5 (GPIO3); also elsewhere on the board
LIMX: U13.9 (GPIO6); also elsewhere on the board
LIMY: U13.7 (GPIO5); also elsewhere on the board
LIMZ: U13.6 (GPIO4); also elsewhere on the board
MIST: U15.6 (QG); also elsewhere on the board
unnamed: R22.1, U14.14 (A)
unnamed: R23.1, U14.12 (LCK)
unnamed: R24.1, U14.11 (SCK)
unnamed: R25.1, U15.14 (A)
unnamed: R26.1, U15.12 (LCK), U16.12 (LCK)
unnamed: R27.1, U15.11 (SCK), U16.11 (SCK)
unnamed: U15.9 (SQH), U16.14 (A)
unnamed: JP4.2, U16.7 (GH)
PRB: U13.34 (GPIO28_ADC2); also elsewhere on the board
RESET: U13.29 (GPIO22); also elsewhere on the board
RUN: C4.1, J15.1, R21.2, SW1.2 (B), U13.30 (RUN)
RX: U13.2 (GPIO1); also elsewhere on the board
SCL: U13.27 (GPIO21); also elsewhere on the board
SDA: U13.26 (GPIO20); also elsewhere on the board
SPDI: U15.4 (QE); also elsewhere on the board
SPEN: U15.5 (QF); also elsewhere on the board
SPI1_CS: U13.17 (GPIO13); also elsewhere on the board
SPI1_RX: U13.16 (GPIO12); also elsewhere on the board
SPI1_SCK: U13.14 (GPIO10); also elsewhere on the board
SPI1_TX: U13.15 (GPIO11); also elsewhere on the board
SPWM: U13.32 (GPIO27_ADC1); also elsewhere on the board
SR0_LCK: R26.2, U13.25 (GPIO19)
SR0_OUT: R25.2, U13.22 (GPIO17)
SR0_SCK: R27.2, U13.24 (GPIO18)
SR1_LCK: R23.2, U13.21 (GPIO16)
SR1_OUT: R22.2, U13.19 (GPIO14)
SR1_SCK: R24.2, U13.20 (GPIO15)
STENA: U15.3 (QD); also elsewhere on the board
STENX: U15.15 (QA); also elsewhere on the board
STENY: U15.1 (QB); also elsewhere on the board
STENZ: U15.2 (QC); also elsewhere on the board
STPA: U14.3 (QD); also elsewhere on the board
STPX: U14.15 (QA); also elsewhere on the board
STPY: U14.1 (QB); also elsewhere on the board
STPZ: U14.2 (QC); also elsewhere on the board
TX: U13.1 (GPIO0); also elsewhere on the board
TXEN: U13.4 (GPIO2); also elsewhere on the board
VBUS: U13.40 (VBUS); also elsewhere on the board
WZ_RST: JP4.1; also elsewhere on the board

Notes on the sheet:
Config Aux7 or W5500 Reset Default W5500
Reset Switch. verify assembly house switch choices.
Shift registers are used to get around the GPIO limitations of the RP2040.
MIT License Copyright (c) 2023, 2025 Phillip L. Barrett Permission is hereby granted, free of charge, to any person obtaining a copy of this software and associated documentation files (the "Software"), to deal in the Software without restriction, including without limitation the rights to use, cop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
Bulk output Shift Register. Used for outputs that are not highly time critical.
High speed Step/Dir shift register for time critical outputs.
Header for external reset switch

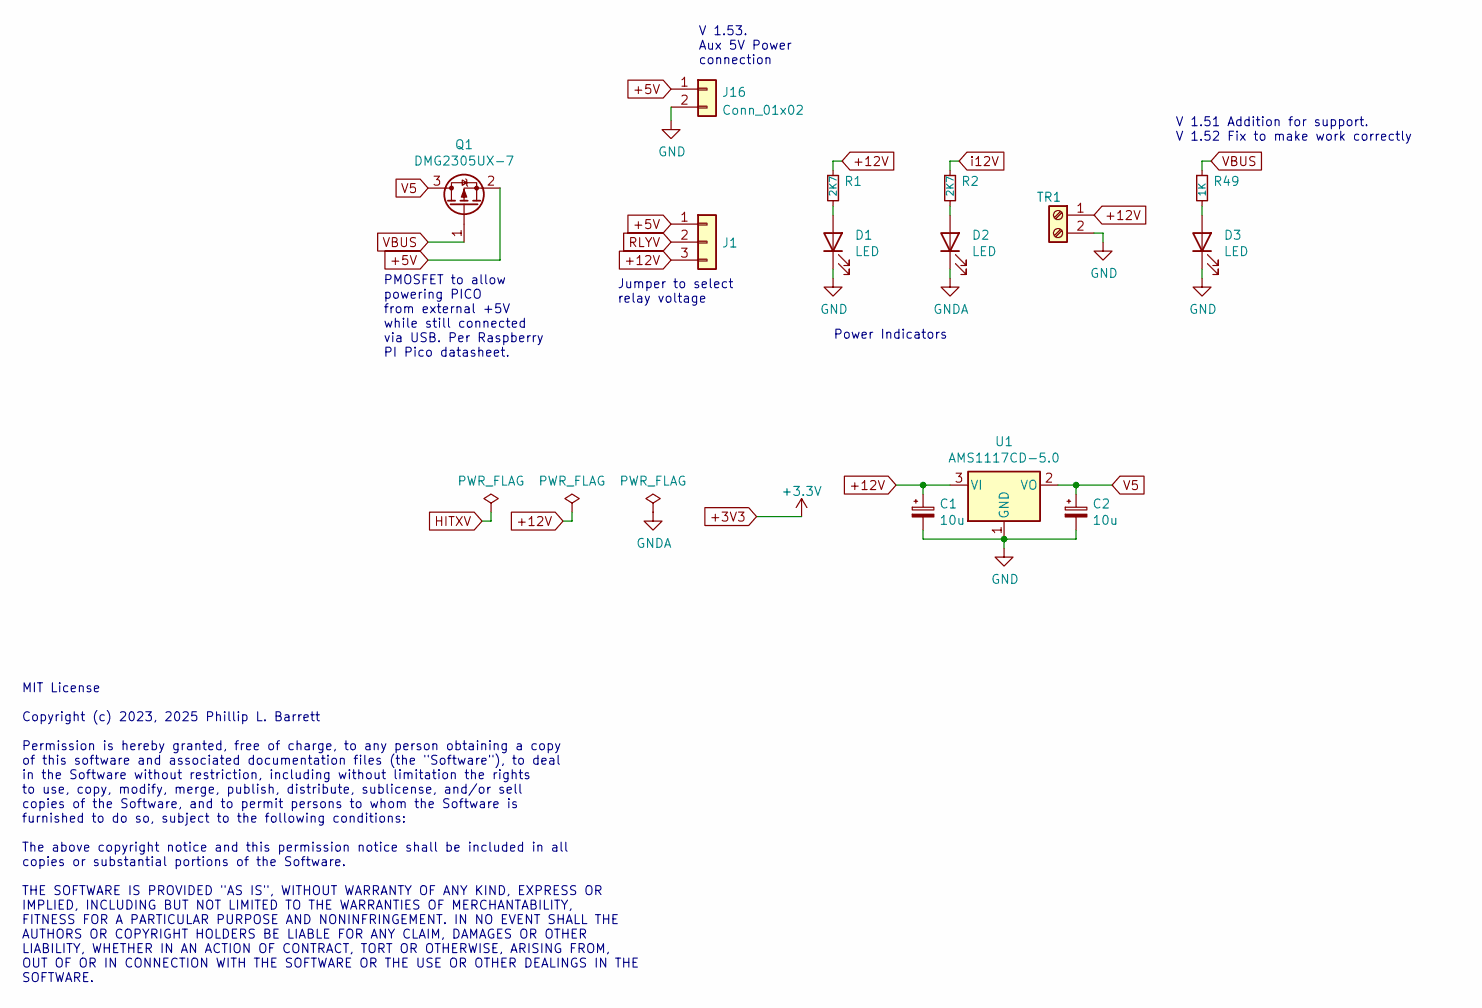
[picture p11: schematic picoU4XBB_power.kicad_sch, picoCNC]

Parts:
C1, C2: 10u; C_0805_2012Metric; LCSC C15850
D1, D2, D3: LED; LED_0805_2012Metric; LCSC C2297
J1: Conn_01x03; 1X03
J16: Conn_01x02; 1X02
Q1: DMG2305UX-7; SOT-23-rct; LCSC C150470
R1, R2: 2K7; R_0603_1608Metric; LCSC C13167
R49: 1K; R_0603_1608Metric; LCSC C21190
TR1: pterm3.5-2; T35-2-5milh; LCSC C409115
U1: AMS1117CD-5.0; SOT-223-3_TabPin2; LCSC C277893

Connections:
+5V: J1.1, J16.1, Q1.2 (S); also elsewhere on the board
+12V: C1.1, J1.3, R1.1, TR1.1, U1.3 (VI); also elsewhere on the board
GND: C1.2, C2.2, D1.1 (K), D3.1 (K), J16.2, TR1.2, U1.1 (GND); also elsewhere on the board
GNDA: D2.1 (K); also elsewhere on the board
unnamed: D1.2 (A), R1.2
unnamed: D2.2 (A), R2.2
unnamed: D3.2 (A), R49.2
RLYV: J1.2; also elsewhere on the board
V5: C2.1, Q1.3 (D), U1.2 (VO)
VBUS: Q1.1 (G), R49.1; also elsewhere on the board
i12V: R2.1; also elsewhere on the board

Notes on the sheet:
V 1.53. Aux 5V Power connection
Power Indicators
Jumper to select relay voltage
V 1.51 Addition for support. V 1.52 Fix to make work correctly
MIT License Copyright (c) 2023, 2025 Phillip L. Barrett Permission is hereby granted, free of charge, to any person obtaining a copy of this software and associated documentation files (the "Software"), to deal in the Software without restriction, including without limitation the rights to use, cop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
PMOSFET to allow powering PICO from external +5V while still connected via USB. Per Raspberry PI Pico datasheet.

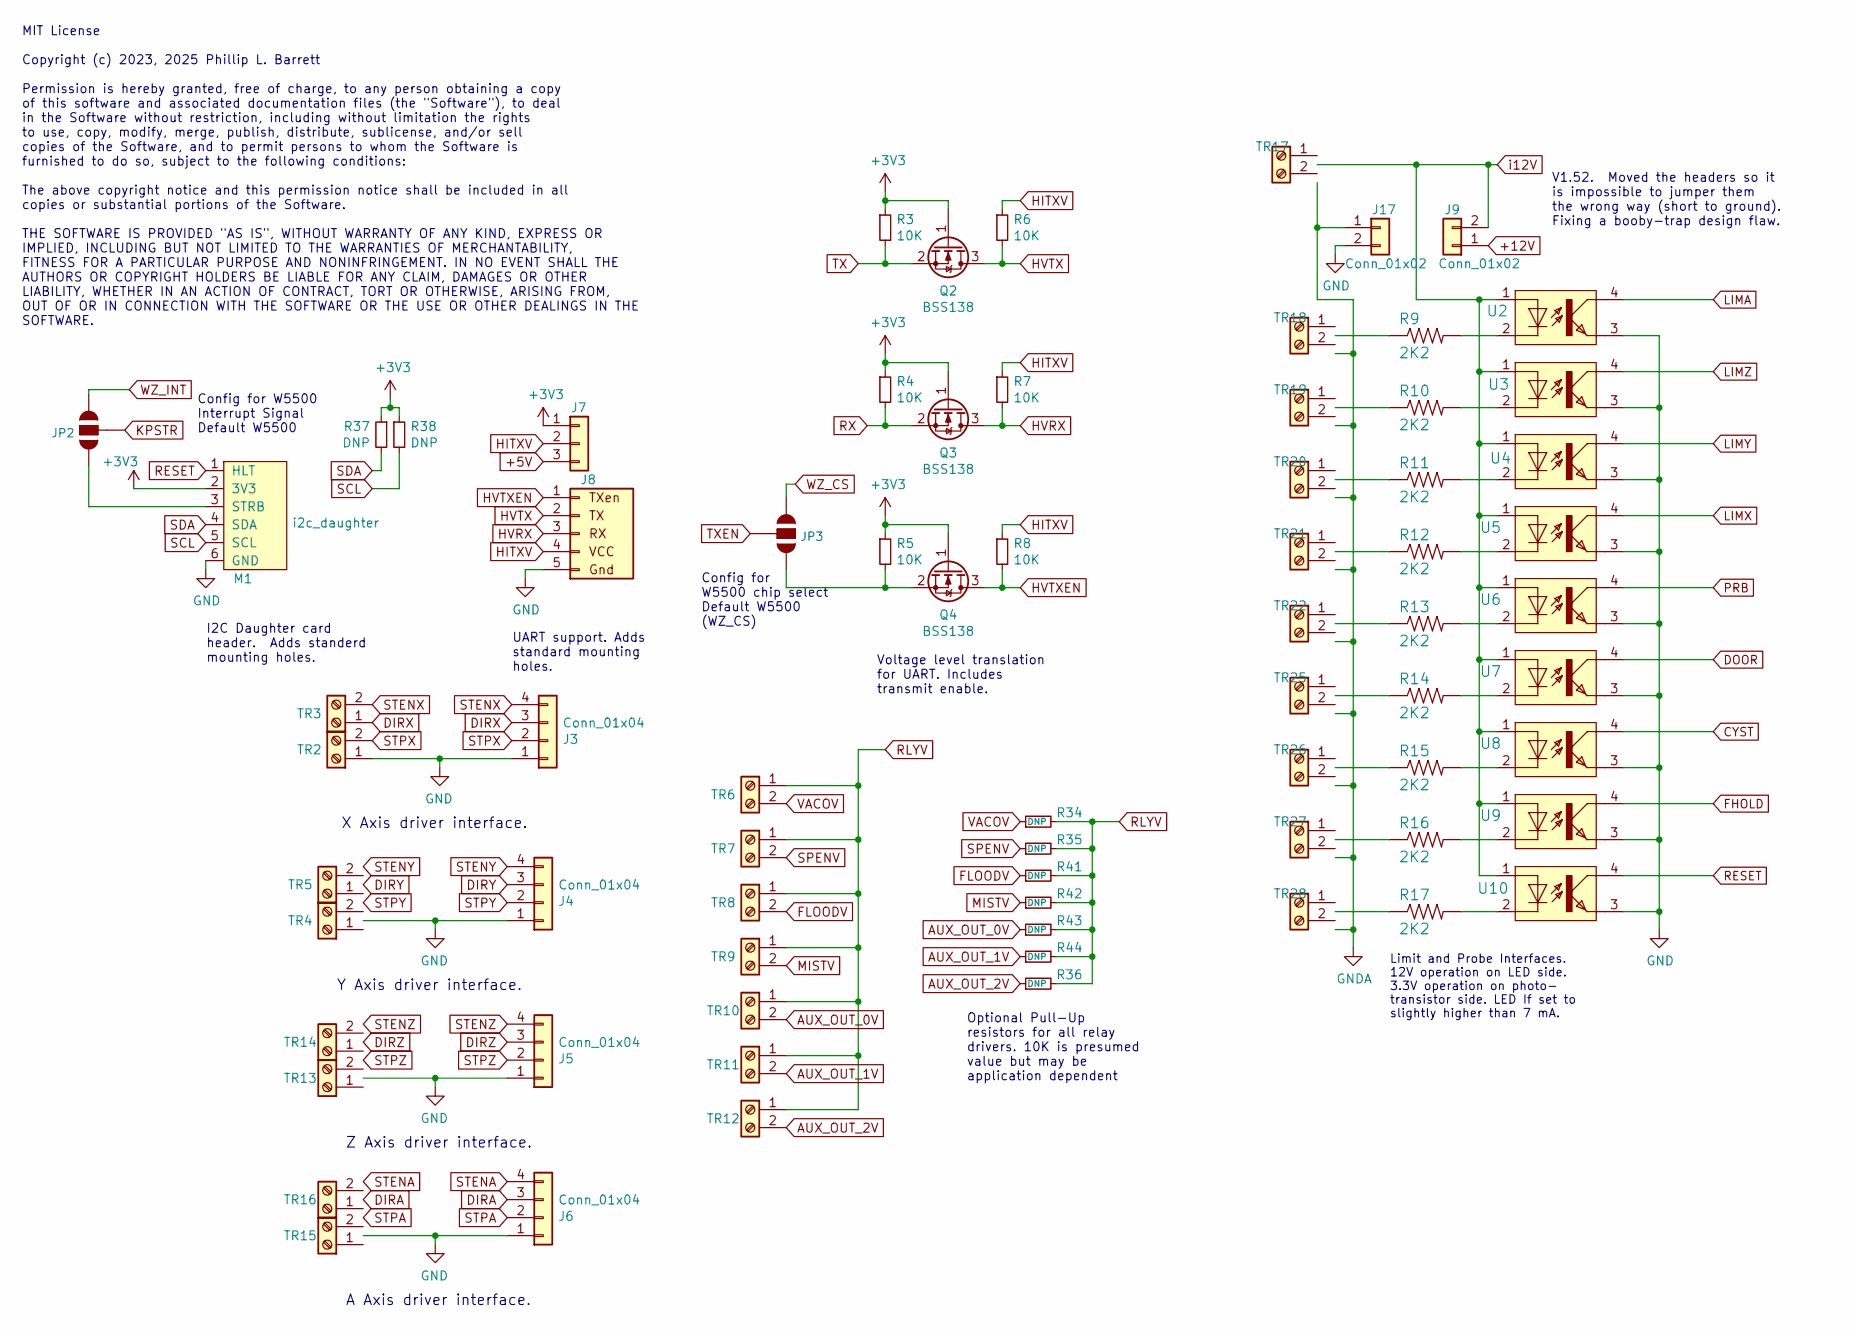
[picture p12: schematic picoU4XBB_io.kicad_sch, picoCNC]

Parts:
J3, J4, J5, J6: Conn_01x04; 1X04
J7: Conn_01x03; 1X03
J8: async_daughter; Serial_header_mountin_holes
J9: Conn_01x02; 1X02-1mm
J17: Conn_01x02; 1X02
JP2, JP3: JUMPER-SMT_3_NO_NO-SILK; SolderJumper-3_P1.3mm_Bridged12_Pad1.0x1.5mm
M1: i2c_daughter; I2C_Header
Q2, Q3, Q4: BSS138; SOT-23-rct; LCSC C40912
R3, R4, R5, R6, R7, R8: 10K; R_0603_1608Metric; LCSC C25804
R9, R10, R11, R12, R13, R14, R15, R16, R17: 2K2; R_0603_1608Metric; LCSC C4190
R34, R35, R36, R41, R42, R43, R44: DNP; R_0805_2012Metric_Pad1.20x1.40mm_HandSolder; LCSC DNP
R37, R38: DNP; R_0805_2012Metric; LCSC C17520
TR2, TR3, TR4, TR5, TR6, TR7, TR8, TR9, TR10, TR11, TR12, TR13, TR14, TR15, TR16, TR17, TR18, TR19, TR20, TR21, TR22, TR25, TR26, TR27, TR28: pterm3.5-2; T35-2-5milh; LCSC C409115
U2, U3, U4, U5, U6, U7, U8, U9, U10: EL3H7-G; LCSC C92243

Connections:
+5V: J7.3; also elsewhere on the board
+12V: J9.1; also elsewhere on the board
AUX0V: R43.1, TR10.2; also elsewhere on the board
AUX1V: R44.1, TR11.2; also elsewhere on the board
AUX2V: R36.1, TR12.2; also elsewhere on the board
CYST: U8.4 (COL); also elsewhere on the board
DIRA: J6.3, TR16.1; also elsewhere on the board
DIRX: J3.3, TR3.1; also elsewhere on the board
DIRY: J4.3, TR5.1; also elsewhere on the board
DIRZ: J5.3, TR14.1; also elsewhere on the board
DOOR: U7.4 (COL); also elsewhere on the board
FHOLD: U9.4 (COL); also elsewhere on the board
FLOODV: R41.1, TR8.2; also elsewhere on the board
GND: J3.1, J4.1, J5.1, J6.1, J8.5 (Gnd), J17.2, M1.6 (GND), TR2.1, TR4.1, TR13.1, TR15.1, U2.3 (EMIT), U3.3 (EMIT), U4.3 (EMIT), U5.3 (EMIT), U6.3 (EMIT), U7.3 (EMIT), U8.3 (EMIT), U9.3 (EMIT), U10.3 (EMIT); also elsewhere on the board
GNDA: J17.1, TR17.2, TR18.2, TR19.2, TR20.2, TR21.2, TR22.2, TR25.2, TR26.2, TR27.2, TR28.2; also elsewhere on the board
HITXV: J7.2, J8.4 (VCC), R6.1, R7.1, R8.1
HVRX: J8.3 (RX), Q3.3 (D), R7.2
HVTX: J8.2 (TX), Q2.3 (D), R6.2
HVTXEN: J8.1 (TXen), Q4.3 (D), R8.2
KPSTR: JP2.2; also elsewhere on the board
LIMA: U2.4 (COL); also elsewhere on the board
LIMX: U5.4 (COL); also elsewhere on the board
LIMY: U4.4 (COL); also elsewhere on the board
LIMZ: U3.4 (COL); also elsewhere on the board
MISTV: R42.1, TR9.2; also elsewhere on the board
unnamed: JP2.3, M1.3 (STRB)
unnamed: JP3.3, Q4.2 (S), R5.2
unnamed: R9.1, TR18.1
unnamed: R10.1, TR19.1
unnamed: R11.1, TR20.1
unnamed: R12.1, TR21.1
unnamed: R13.1, TR22.1
unnamed: R14.1, TR25.1
unnamed: R15.1, TR26.1
unnamed: R16.1, TR27.1
unnamed: R17.1, TR28.1
unnamed: R9.2, U2.2 (C)
unnamed: R10.2, U3.2 (C)
unnamed: R11.2, U4.2 (C)
unnamed: R12.2, U5.2 (C)
unnamed: R13.2, U6.2 (C)
unnamed: R14.2, U7.2 (C)
unnamed: R15.2, U8.2 (C)
unnamed: R16.2, U9.2 (C)
unnamed: R17.2, U10.2 (C)
PRB: U6.4 (COL); also elsewhere on the board
RESET: M1.1 (HLT), U10.4 (COL); also elsewhere on the board
RLYV: R34.2, R35.2, R36.2, R41.2, R42.2, R43.2, R44.2, TR6.1, TR7.1, TR8.1, TR9.1, TR10.1, TR11.1, TR12.1; also elsewhere on the board
RX: Q3.2 (S), R4.2; also elsewhere on the board
SCL: M1.5 (SCL), R38.2; also elsewhere on the board
SDA: M1.4 (SDA), R37.2; also elsewhere on the board
SPENV: R35.1, TR7.2; also elsewhere on the board
STENA: J6.4, TR16.2; also elsewhere on the board
STENX: J3.4, TR3.2; also elsewhere on the board
STENY: J4.4, TR5.2; also elsewhere on the board
STENZ: J5.4, TR14.2; also elsewhere on the board
STPA: J6.2, TR15.2; also elsewhere on the board
STPX: J3.2, TR2.2; also elsewhere on the board
STPY: J4.2, TR4.2; also elsewhere on the board
STPZ: J5.2, TR13.2; also elsewhere on the board
TX: Q2.2 (S), R3.2; also elsewhere on the board
TXEN: JP3.2; also elsewhere on the board
VACOV: R34.1, TR6.2; also elsewhere on the board
WZ_CS: JP3.1; also elsewhere on the board
WZ_INT: JP2.1; also elsewhere on the board
i12V: J9.2, TR17.1, U2.1 (A), U3.1 (A), U4.1 (A), U5.1 (A), U6.1 (A), U7.1 (A), U8.1 (A), U9.1 (A), U10.1 (A); also elsewhere on the board

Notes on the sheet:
X Axis driver interface.
Z Axis driver interface.
UART support. Adds standard mounting holes.
Limit and Probe Interfaces. 12V operation on LED side. 3.3V operation on photo- transistor side. LED If set to slightly higher than 7 mA.
MIT License Copyright (c) 2023, 2025 Phillip L. Barrett Permission is hereby granted, free of charge, to any person obtaining a copy of this software and associated documentation files (the "Software"), to deal in the Software without restriction, including without limitation the rights to use, cop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
Voltage level translation for UART. Includes transmit enable.
Optional Pull-Up resistors for all relay drivers. 10K is presumed value but may be application dependent
A Axis driver interface.
Y Axis driver interface.
I2C Daughter card header. Adds standerd mounting holes.
Config for W5500 chip select Default W5500 (WZ_CS)
V1.52. Moved the headers so it is impossible to jumper them the wrong way (short to ground). Fixing a booby-trap design flaw.
Config for W5500 Interrupt Signal Default W5500

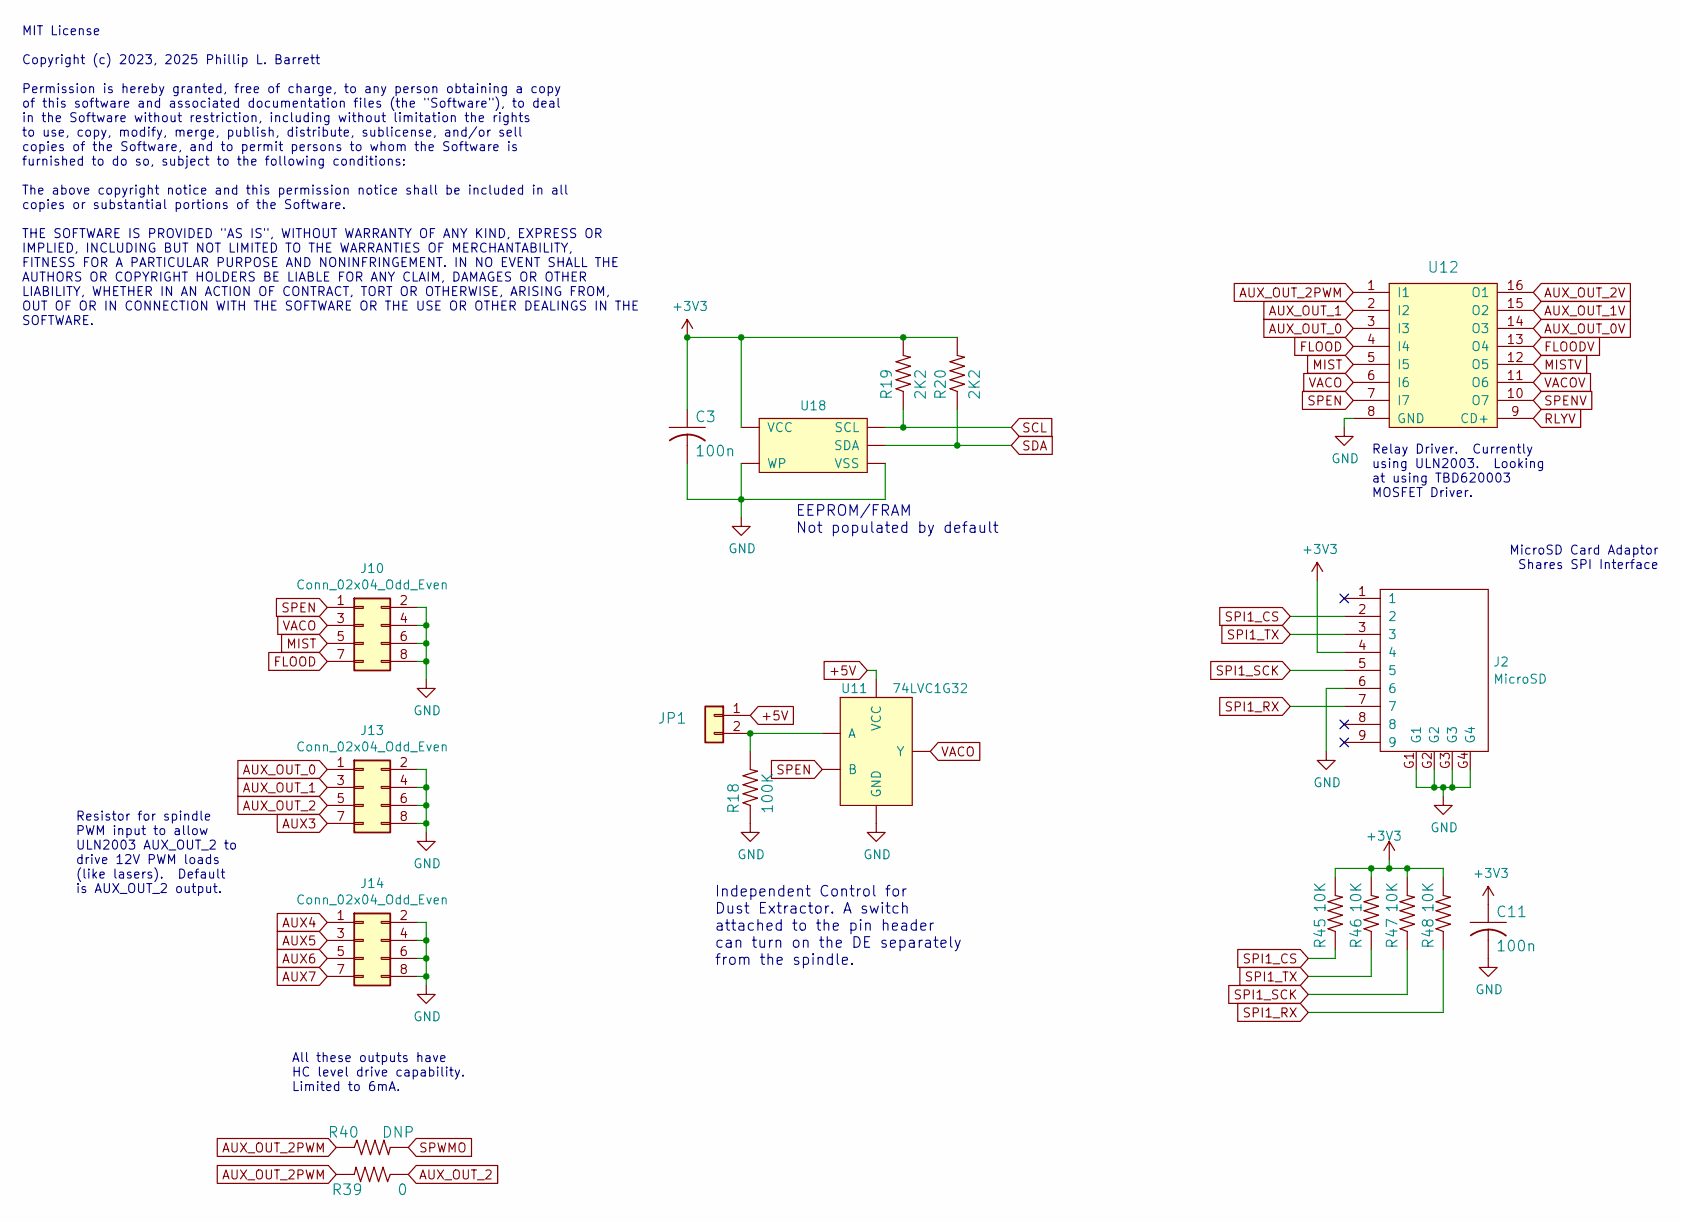
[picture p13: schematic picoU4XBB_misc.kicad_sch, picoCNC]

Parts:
C3, C11: 100n; C_0805_2012Metric; LCSC C49678
J2: MicroSD
J10, J13, J14: Conn_02x04_Odd_Even; 2X04
JP1: PINHD-1X2; 1X02; LCSC C358684
R18: 100K; R_0603_1608Metric; LCSC C25803
R19, R20: 2K2; R_0603_1608Metric; LCSC C4190
R39: 0; R_0805_2012Metric; LCSC C17477
R40: DNP; R_0805_2012Metric; LCSC C17407
R45, R46, R47, R48: 10K; R_0603_1608Metric; LCSC C25804
U11: 74LVC1G32; SOT-353_SC-70-5; LCSC C460530
U12: ULN2003AD; SO16; LCSC C7512
U18: FM24CLxxx; SO08

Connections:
+5V: JP1.1, U11.5 (VCC); also elsewhere on the board
AUX0: J13.1, U12.3 (I3); also elsewhere on the board
AUX0V: U12.14 (O3); also elsewhere on the board
AUX1: J13.3, U12.2 (I2); also elsewhere on the board
AUX1V: U12.15 (O2); also elsewhere on the board
AUX2: J13.5, R39.1; also elsewhere on the board
AUX2PWM: R39.2, R40.1, U12.1 (I1)
AUX2V: U12.16 (O1); also elsewhere on the board
AUX3: J13.7; also elsewhere on the board
AUX4: J14.1; also elsewhere on the board
AUX5: J14.3; also elsewhere on the board
AUX6: J14.5; also elsewhere on the board
AUX7: J14.7; also elsewhere on the board
FLOOD: J10.7, U12.4 (I4); also elsewhere on the board
FLOODV: U12.13 (O4); also elsewhere on the board
GND: C3.2, C11.2, J2.6, J2.G1, J2.G2, J2.G3, J2.G4, J2.MP1, J2.MP2, J2.MP3, J2.MP4, J10.2, J10.4, J10.6, J10.8, J13.2, J13.4, J13.6, J13.8, J14.2, J14.4, J14.6, J14.8, R18.1, U11.3 (GND), U12.8 (GND), U18.4 (VSS), U18.7 (WP); also elsewhere on the board
MIST: J10.5, U12.5 (I5); also elsewhere on the board
MISTV: U12.12 (O5); also elsewhere on the board
unnamed: JP1.2, R18.2, U11.1 (A)
RLYV: U12.9 (CD+); also elsewhere on the board
SCL: R19.1, U18.6 (SCL); also elsewhere on the board
SDA: R20.1, U18.5 (SDA); also elsewhere on the board
SPEN: J10.1, U11.2 (B), U12.7 (I7); also elsewhere on the board
SPENV: U12.10 (O7); also elsewhere on the board
SPI1_CS: J2.2, R45.1; also elsewhere on the board
SPI1_RX: J2.7, R48.1; also elsewhere on the board
SPI1_SCK: J2.5, R47.1; also elsewhere on the board
SPI1_TX: J2.3, R46.1; also elsewhere on the board
SPWMO: R40.2; also elsewhere on the board
VACO: J10.3, U11.4 (Y), U12.6 (I6)
VACOV: U12.11 (O6); also elsewhere on the board

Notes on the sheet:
MicroSD Card Adaptor Shares SPI Interface
All these outputs have HC level drive capability. Limited to 6mA.
EEPROM/FRAM Not populated by default
Resistor for spindle PWM input to allow ULN2003 AUX_OUT_2 to drive 12V PWM loads (like lasers). Default is AUX_OUT_2 output.
Relay Driver. Currently using ULN2003. Looking at using TBD620003 MOSFET Driver.
MIT License Copyright (c) 2023, 2025 Phillip L. Barrett Permission is hereby granted, free of charge, to any person obtaining a copy of this software and associated documentation files (the "Software"), to deal in the Software without restriction, including without limitation the rights to use, cop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
Independent Control for Dust Extractor. A switch attached to the pin header can turn on the DE separately from the spindle.

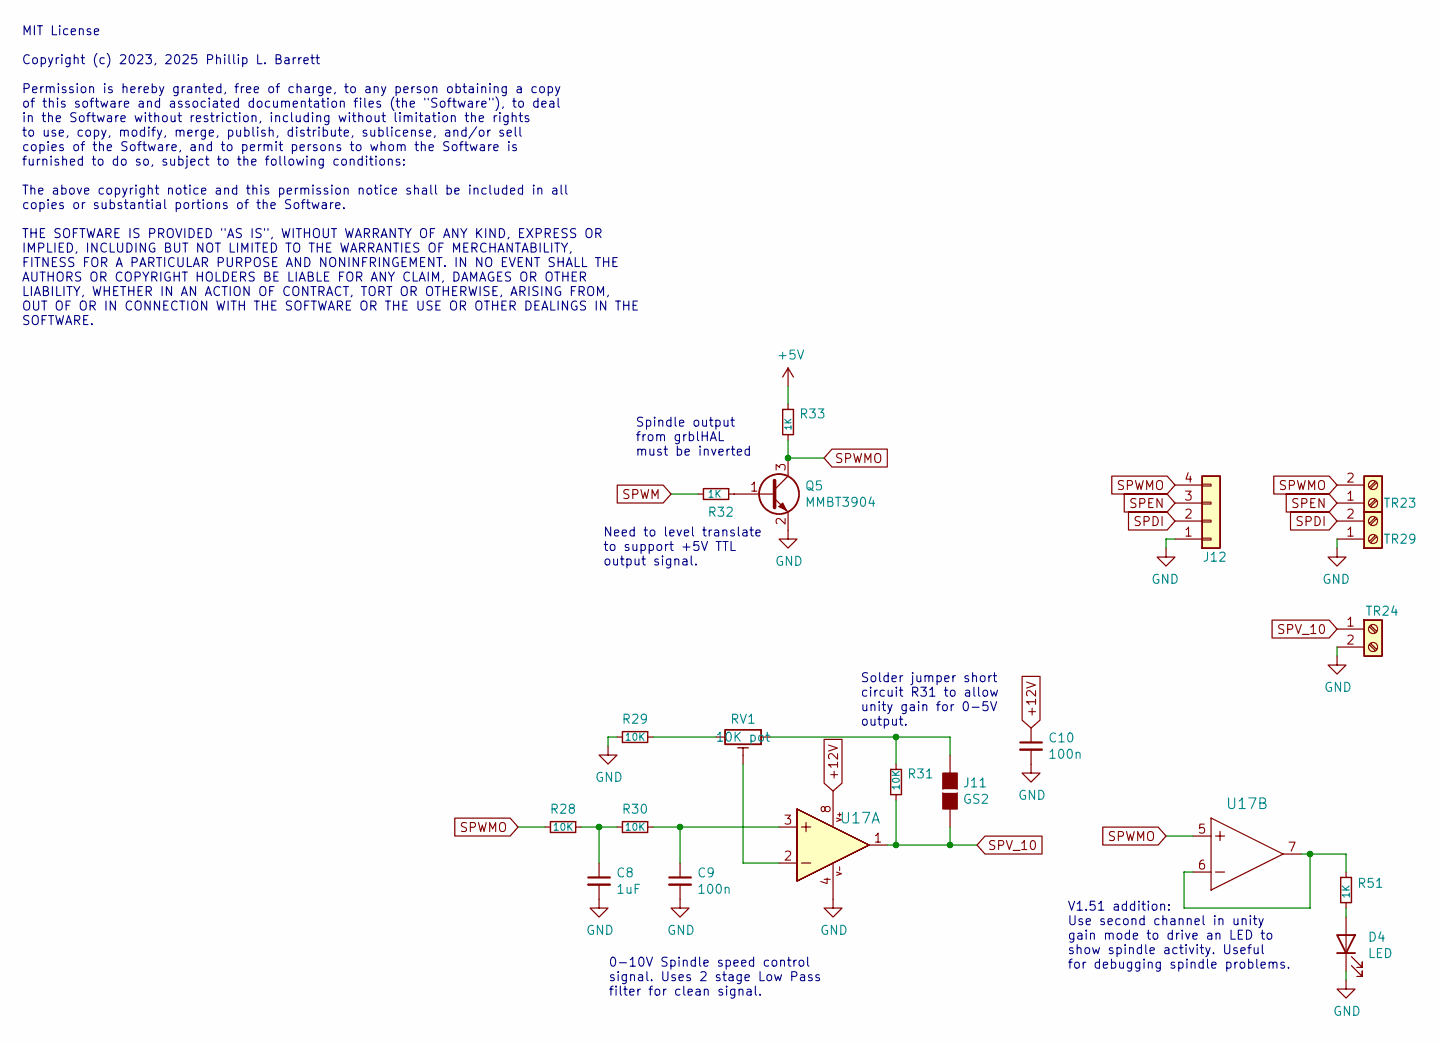
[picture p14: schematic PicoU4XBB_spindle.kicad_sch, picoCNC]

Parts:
C8: 1uF; C_0805_2012Metric; LCSC C28323
C9, C10: 100n; C_0805_2012Metric; LCSC C49678
D4: LED; LED_0805_2012Metric; LCSC C2297
J11: GS2; SolderJumper-2_P1.3mm_Open_RoundedPad1.0x1.5mm
J12: Conn_01x04; 1X04
Q5: MMBT3904; SOT-23-rct; LCSC C20526
R28, R29, R30, R31: 10K; R_0603_1608Metric; LCSC C25804
R32, R33, R51: 1K; R_0603_1608Metric; LCSC C21190
RV1: 10K pot; RM065-trimmer; LCSC C5205021
TR23, TR24, TR29: pterm3.5-2; T35-2-5milh; LCSC C409115
U17: LM358D; SO08; LCSC C2683482

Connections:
+5V: R33.1; also elsewhere on the board
+12V: C10.1, U17.8 (V+); also elsewhere on the board
GND: C8.2, C9.2, C10.2, D4.1 (K), J12.1, Q5.2 (E), R29.2, TR24.2, TR29.1, U17.4 (V-); also elsewhere on the board
unnamed: C8.1, R28.1, R30.2
unnamed: D4.2 (A), R51.2
unnamed: J11.1 (G1), R31.1, RV1.1
unnamed: Q5.1 (B), R32.1
unnamed: R29.1, RV1.3
unnamed: C9.1, R30.1, U17.3 (+IN)
unnamed: RV1.2, U17.2 (-IN)
unnamed: R51.1, U17.6 (-IN), U17.7 (OUT)
SPDI: J12.2, TR29.2; also elsewhere on the board
SPEN: J12.3, TR23.1; also elsewhere on the board
SPV_10: J11.2 (G2), R31.2, TR24.1, U17.1 (OUT)
SPWM: R32.2; also elsewhere on the board
SPWMO: J12.4, Q5.3 (C), R28.2, R33.2, TR23.2, U17.5 (+IN); also elsewhere on the board

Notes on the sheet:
Need to level translate to support +5V TTL output signal.
Solder jumper short circuit R31 to allow unity gain for 0-5V output.
0-10V Spindle speed control signal. Uses 2 stage Low Pass filter for clean signal.
MIT License Copyright (c) 2023, 2025 Phillip L. Barrett Permission is hereby granted, free of charge, to any person obtaining a copy of this software and associated documentation files (the "Software"), to deal in the Software without restriction, including without limitation the rights to use, cop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
Spindle output from grblHAL must be inverted
V1.51 addition: Use second channel in unity gain mode to drive an LED to show spindle activity. Useful for debugging spindle problems.

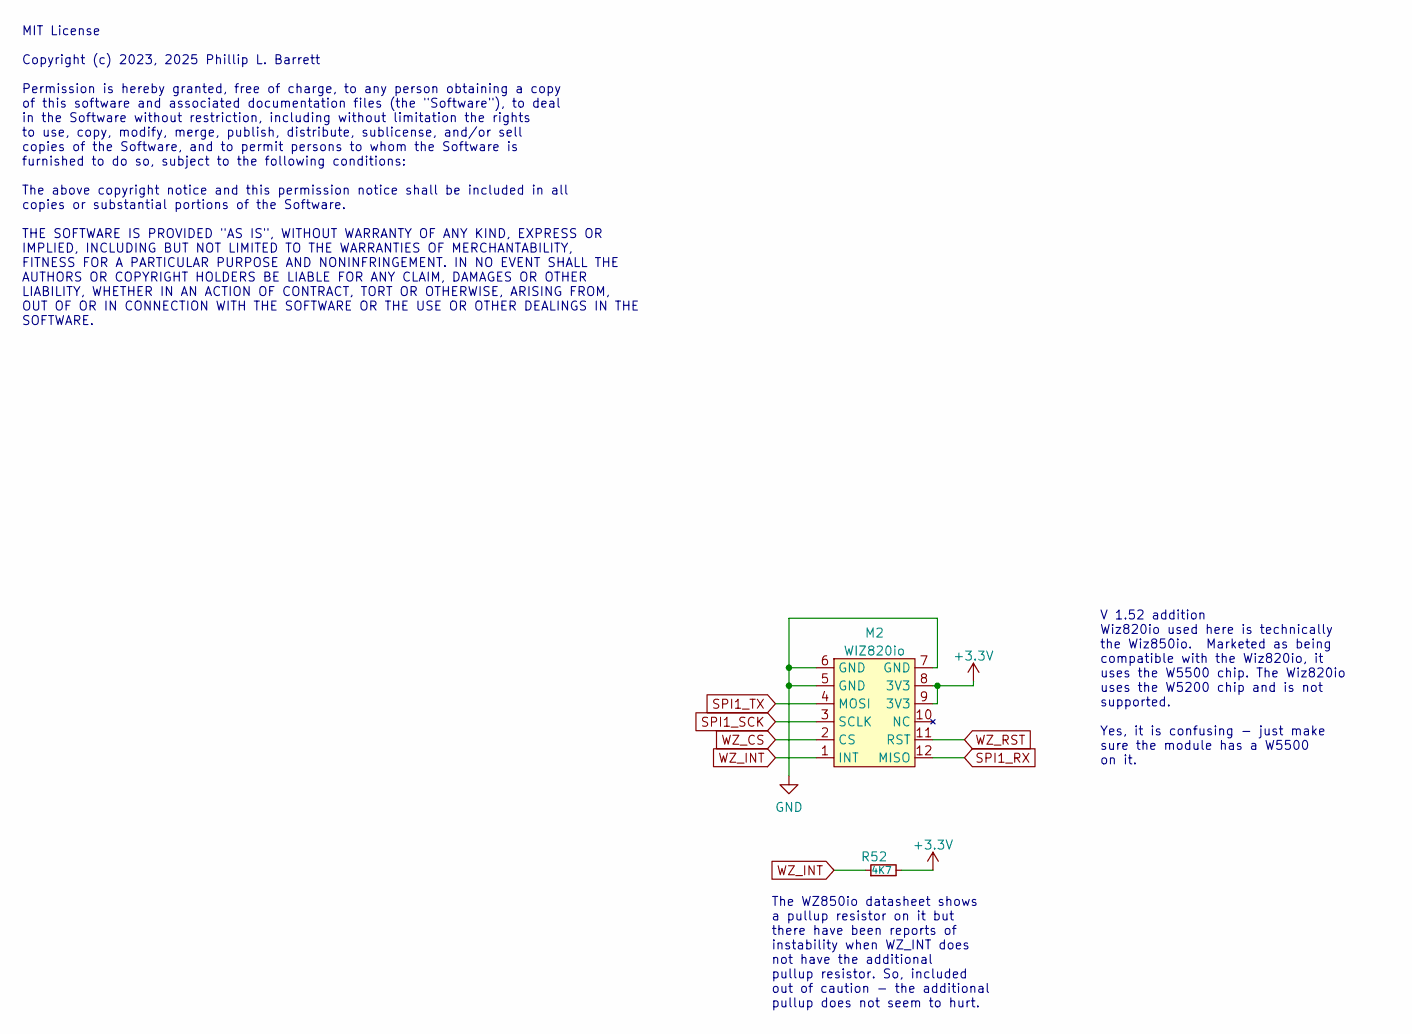
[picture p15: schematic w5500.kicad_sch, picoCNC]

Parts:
M2: WIZ820io; wiz820io
R52: 4K7; R_0603_1608Metric; LCSC C23162

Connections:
GND: M2.5 (GND), M2.6 (GND), M2.7 (GND); also elsewhere on the board
SPI1_RX: M2.12 (MISO); also elsewhere on the board
SPI1_SCK: M2.3 (SCLK); also elsewhere on the board
SPI1_TX: M2.4 (MOSI); also elsewhere on the board
WZ_CS: M2.2 (CS); also elsewhere on the board
WZ_INT: M2.1 (INT), R52.1; also elsewhere on the board
WZ_RST: M2.11 (RST); also elsewhere on the board

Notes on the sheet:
MIT License Copyright (c) 2023, 2025 Phillip L. Barrett Permission is hereby granted, free of charge, to any person obtaining a copy of this software and associated documentation files (the "Software"), to deal in the Software without restriction, including without limitation the rights to use, cop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
The WZ850io datasheet shows a pullup resistor on it but there have been reports of instability when WZ_INT does not have the additional pullup resistor. So, included out of caution - the additional pullup does not seem to hurt.
V 1.52 addition Wiz820io used here is technically the Wiz850io. Marketed as being compatible with the Wiz820io, it uses the W5500 chip. The Wiz820io uses the W5200 chip and is not supported. Yes, it is confusing - just make sure the module has a W5500 on it.

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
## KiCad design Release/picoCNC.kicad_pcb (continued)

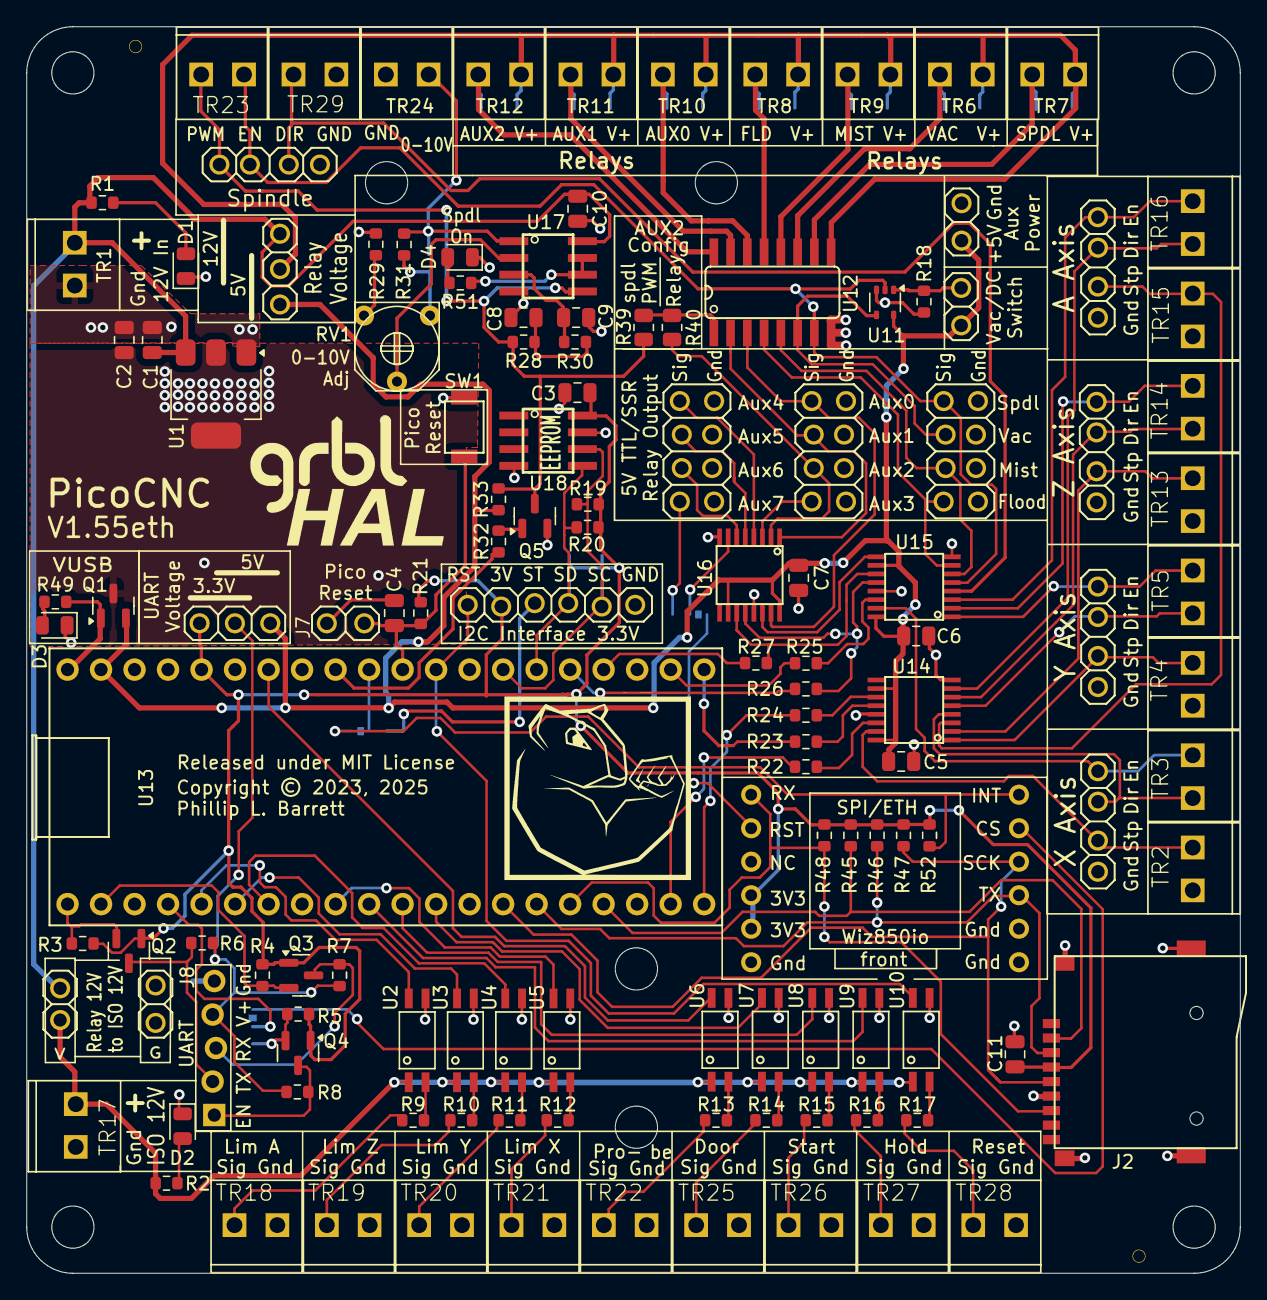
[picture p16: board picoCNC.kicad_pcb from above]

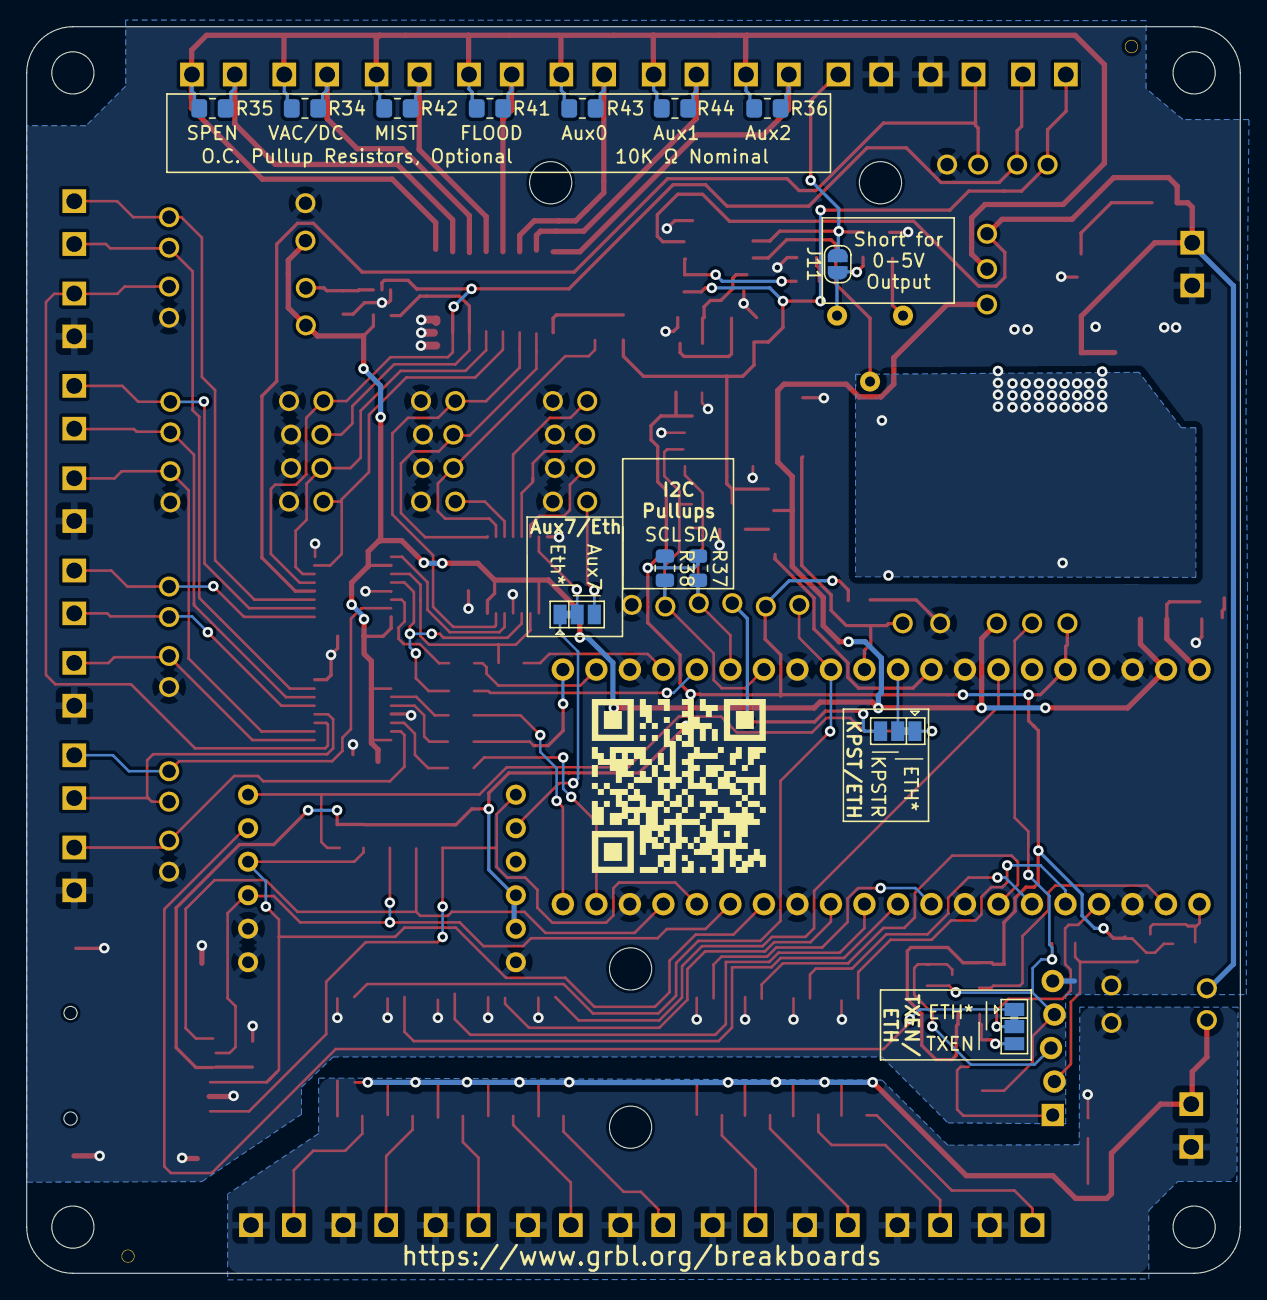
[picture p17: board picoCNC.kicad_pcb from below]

Board: 2 copper layers, 92.0 x 94.5 mm, 145 parts (13 on the bottom side), 118 nets.

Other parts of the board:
A: stencil_align_1mm
A#2: stencil_align_1mm

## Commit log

2023-07-24 Add files via upload
    Photo of V1.5 board
2023-07-28 Add files via upload
    V1.01 - Updated fw install process and initial Grbl Settings. Added errata.
2023-08-25 Add files via upload
    Update to include more assembly photos, document V1.52 differences and minor typo corrections.

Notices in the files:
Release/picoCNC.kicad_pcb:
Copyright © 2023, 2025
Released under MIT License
